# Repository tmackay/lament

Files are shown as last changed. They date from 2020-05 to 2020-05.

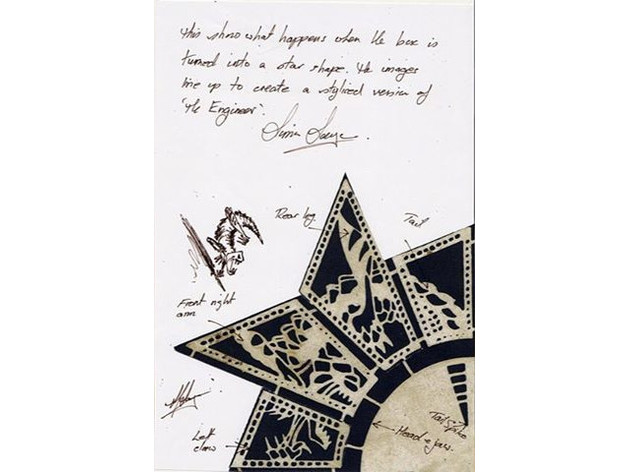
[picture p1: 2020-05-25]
sayce.jpg

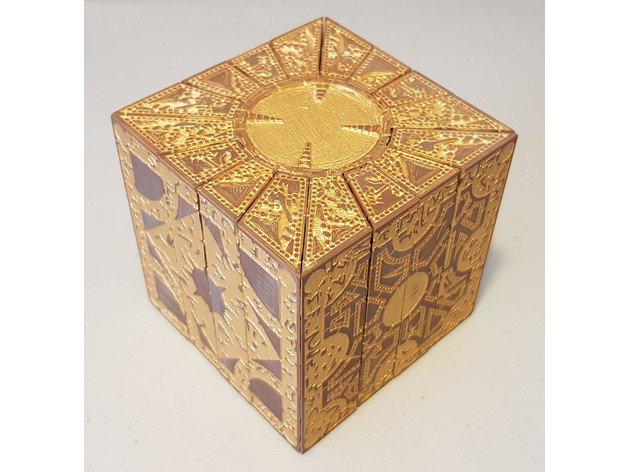
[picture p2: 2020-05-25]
painted.jpg

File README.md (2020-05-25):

# lament
Hellraiser Puzzle Box - Lament Configuration

Functioning Hellraiser inspired puzzle box using my own planetary gearbox core.

[Assembly video](https://youtu.be/JLJvNn56pJ8) - Jump to the end to see the finished product in action. Now tracking my source code in [github](https://github.com/tmackay/lament) to make tracking versions and bugs easier.

The Lament configuration - art by [artist064](https://www.deviantart.com/artist064) "The original Lament Configuration was created by [Simon Sayce](https://www.youtube.com/watch?v=OcX2sYlTq2U) for the original Hellraiser movie".

This is a slight improvement over the previous design which was only solvable by a simplistic brute force method. I have added an extra latch which must be disengaged after aligning the gears. It is also a bit of an experiment in incorporating an internal "clicker" device to indicate when the gears are (partially) aligned. There are also "false gates" which give it away by allowing the core to open slightly when aligned - without these I think it would be near impossible (CH included) unless we incorporate some other indicator (the sound of distant bells, perhaps - there is room for electronics). Also provision for an internal spring to bring the box to "life". If the "clicker" idea works out, it might be worth adding more for effect. Some aluminium strips and magnets could be included in future a future release to provide an inductive braking effect.

Print at 0.2mm (at least the core - it is designed to produce a 1-layer gap between the ring gears and is sensitive to layer height) and separate ring gears with a sharpened spatula, flat razor blade scraper, box cutter or similar. Print parts A and B separately (around 21 hours each, 8 for the core). Ease the core (wider tabs first, careful of orientation and alignment of the narrow tabs) into the end of the "claw", they will need to flex a little.

Enable Support Interface at 100%, Touching Buildplate with overhang of 85 degrees for improved finish. This will give a nice solid disk to support the raised dial for parts A and B which can be pried off. Part C does not require support. (Cura)

I'd also recommend "breaking in" the core by giving it 5 minutes on a drill or Dremel tool to spin the gears. They will be quite stiff at first but soon wear in to move freely. Similarly the sliding parts might need a light sanding or at least operated back and forth a bit to loosen them up.

Bitmaps were converted to black and white using Threshold filter in GIMP then traced using InkScape, simplified using "Flatten Bezziers" extension before being exported as SVG for import into OpenSCAD. OpenSCAD struggled importing multiple SVGs, so individual faces were added to separate cubes and combined using MeshLab ([more info](https://www.thingiverse.com/thing:4178313)).

TinkerCad was used for the final intersection (subtract the negative from the artwork cube) as everything else I tried crashed or made a mess of the mesh.

Most versions of this artwork have the gold detail raised, personally I prefer the negative as it preserves most visual detail when slicing for FDM. Painting gold followed by sanding back the raised edges allows for low painting skill required. If you'd like to try other artwork cubes, I have included the negative. Load your own cube in TinkerCad, scale as desired and subtract. The two halves can then be separated in MeshLab or similar for printing (eg. using select connected followed by delete).

I've also just realised all the artwork is in mirror image in previous versions, betrayed by "The Beautiful Woman", "The Crouching Man" et al. The orientation of the faces relative to each other is also incorrect. I have attempted to remain faithful to the original design, however it is apparent that multiple on-screen props were used with differing configurations, even some faces mirrored. To this end I have settled on the widely used [HR1 configuration by Xane](http://www.cenobite.com/box/lament/)

The latest upload is also dimensionally accurate with the original being 3" across exactly (according to the interview with Sayce) which "held some significance" as opposed to the 80mm approximations. I have also included both positive and negative versions of the artwork to cater to different painting/finishing preferences.

UPDATE: Fixed some overlap in the core which was causing it to print the planet gears fused to the ring gears more so than expected. Still working on the spring idea - will probably go back to a shorter spring contained within the center of the core.

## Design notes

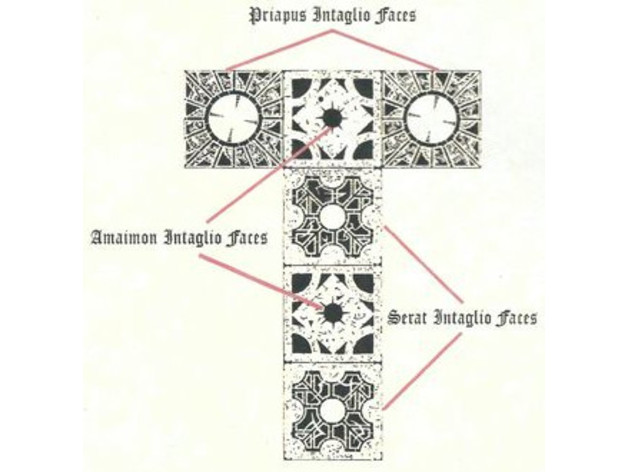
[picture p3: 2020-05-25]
flat.jpg

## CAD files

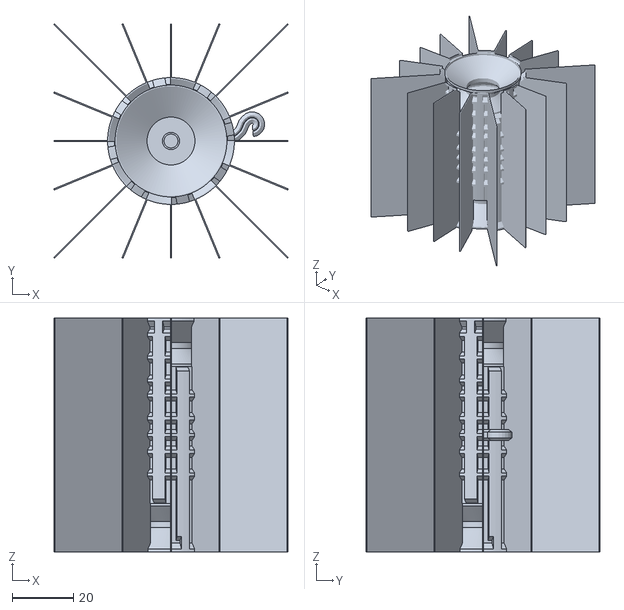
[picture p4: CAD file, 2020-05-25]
Puzzle_Cube_3x3N.stl
76.2 x 76.2 x 76.2

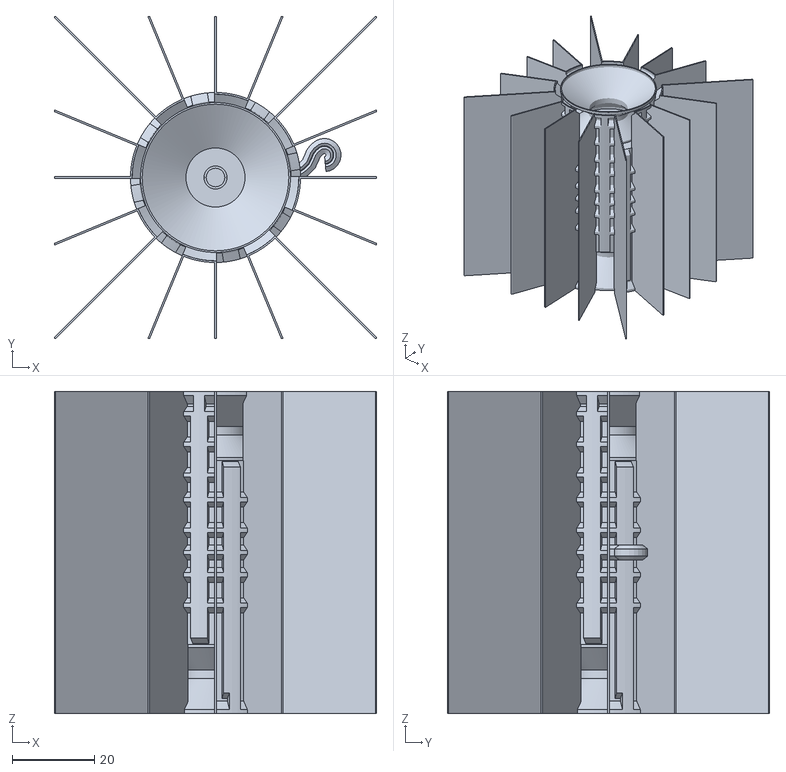
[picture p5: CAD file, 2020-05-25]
Puzzle_Cube_3x3P.stl
78.2 x 78.2 x 78.2

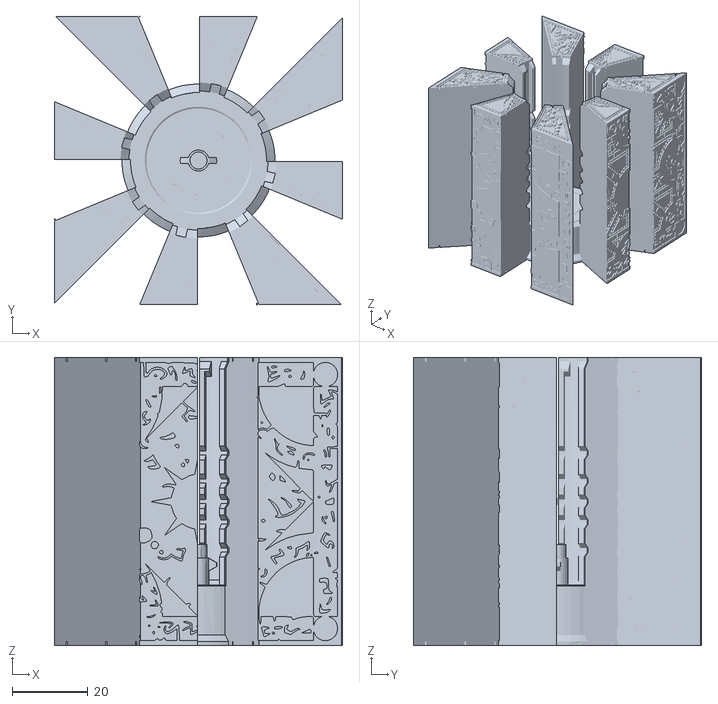
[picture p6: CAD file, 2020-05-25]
Lament_Configuration_3x3x3_Negative_B.stl
76.2 x 76.2 x 76.2

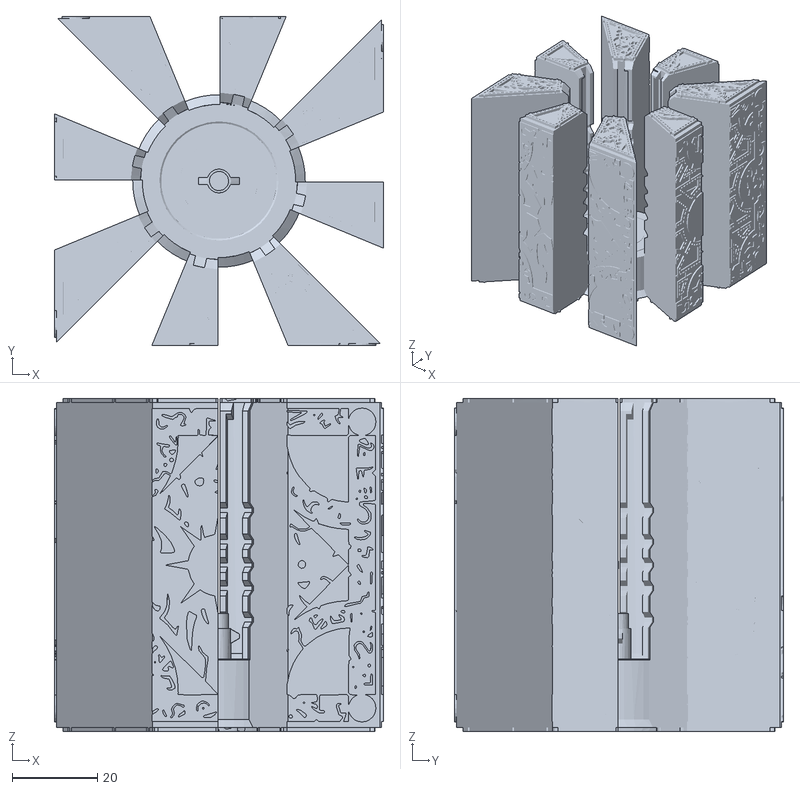
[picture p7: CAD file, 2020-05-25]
Lament_Configuration_3x3x3_Positive_B.stl
77.2 x 77.2 x 78.2

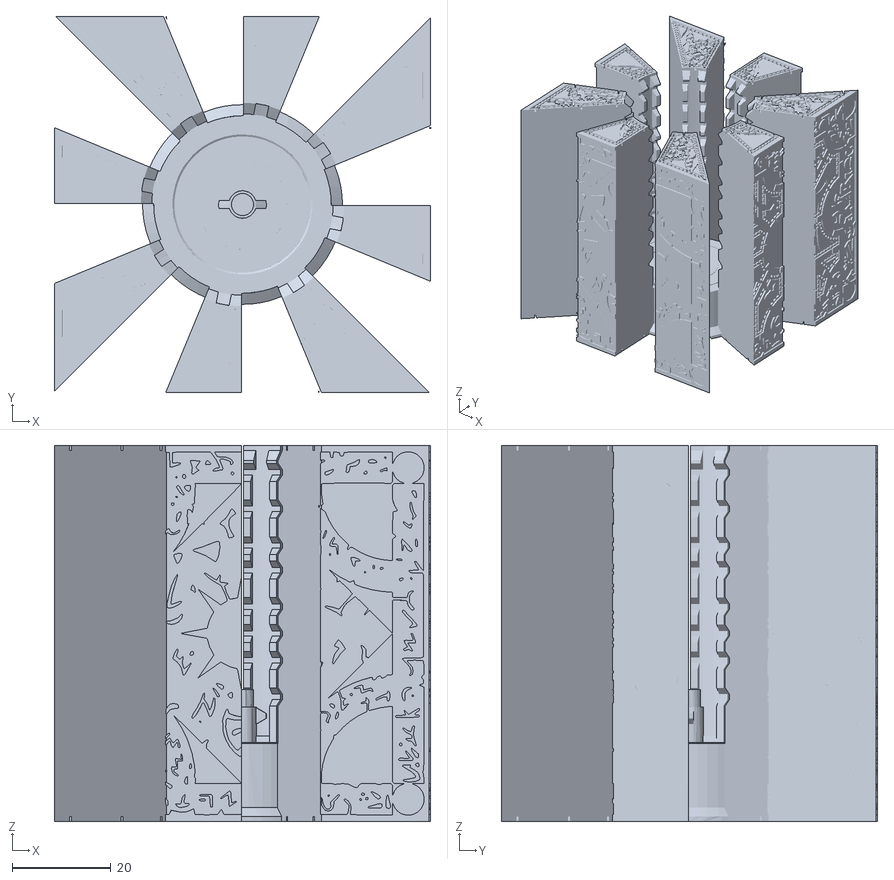
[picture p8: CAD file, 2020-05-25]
Lament_Configuration_3x3x3_Negative_A.stl
76.2 x 76.2 x 76.2

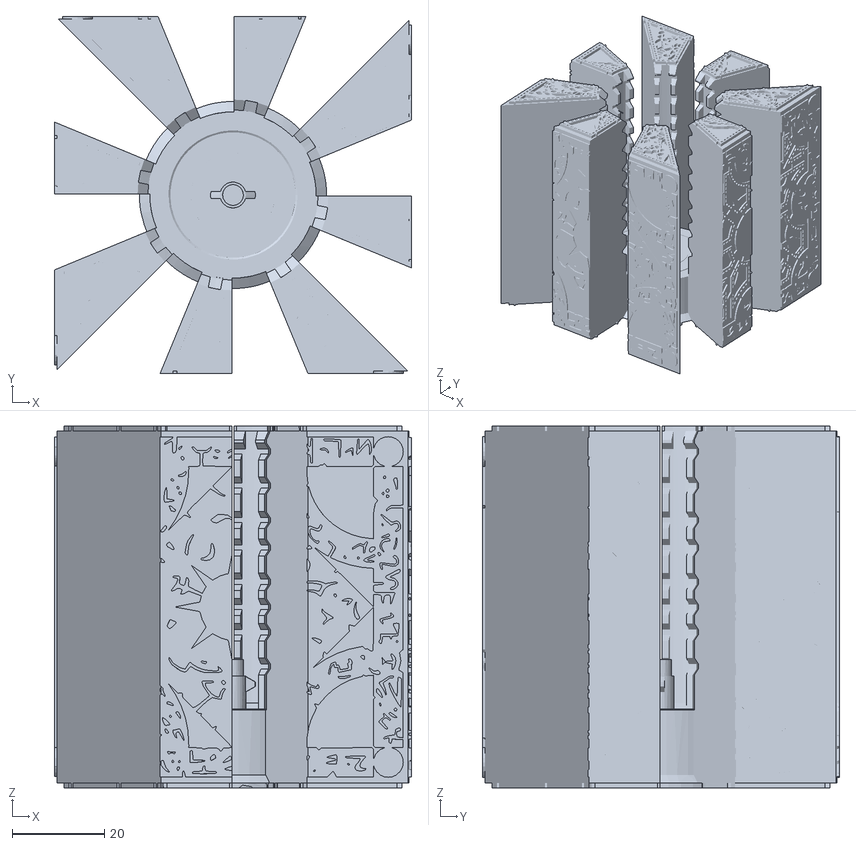
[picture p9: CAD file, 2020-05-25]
Lament_Configuration_3x3x3_Positive_A.stl
77.2 x 77.2 x 78.2

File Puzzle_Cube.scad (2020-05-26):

// OpenSCAD Compound Planetary System
// (c) 2019, tmackay
//
// Licensed under a Creative Commons Attribution-ShareAlike 4.0 International (CC BY-SA 4.0) license, http://creativecommons.org/licenses/by-sa/4.0.
//include <MCAD/involute_gears.scad> 

// Which one would you like to see?
part = "core"; // [box:Box,lower:Lower Half,upper:Upper Half,core:Core]

// Use for command line option '-Dgen=n', overrides 'part'
// 0-7+ - generate parts individually in assembled positions. Combine with MeshLab.
// 0 box
// 1 ring gears and jaws
// 2 sun gear and knob
// 3+ planet gears
gen=undef;

/*
P1	P2	R1	R2	S1=2*P1	S2=2*P2	n1	n2	Gear Ratio
8	5	34	20	16	10	-2	0	-38.66666667
8	6	34	23	16	12	-2	1	-22.23333333
8	7	34	26	16	14	-2	2	-16.75555556
*/

// Overall scale (to avoid small numbers, internal faces or non-manifold edges)
scl = 1000;

// External dimensions of cube
cube_w_ = 76.2;
cube_w = cube_w_*scl;

// Number of planet gears in inner circle
planets = 5; //[3:1:21]

// Height of planetary layers (layer_h will be subtracted from gears>0)
gh_ = [7.2, 7.4, 7.4, 7.4, 7.4, 7.4];
gh = scl*gh_;
// Modules, planetary layers
modules = len(gh); //[2:1:3]

// Number of teeth in planet gears
pt = [5, 6, 7, 7, 6, 5];
// For additional gear ratios we can add or subtract extra teeth (in multiples of planets) from rings but the profile will be further from ideal
of = 0*gh_;
// number of teeth to twist across
nt = pt/pt[0];
// Sun gear multiplier
sgm = 2; //[1:1:5]
// For fused sun gears, we require them to be a multiple of the planet teeth
dt = pt*sgm;
// Find closest ring gear to ideal
// and add offset
rt = [for(i=[0:modules-1])round((2*dt[i]+2*pt[i])/planets+of[i])*planets-dt[i]];
// Outer diameter of core
outer_d_ = 36.0; //[30:0.2:300]
outer_d = scl*outer_d_;
// Ring wall thickness (relative pitch radius)
wall_ = 3.1; //[0:0.1:20]
wall = scl*wall_;

// Hollow - might actually increase print time but could help for SLA
Hollow = 0;				// [1:Yes , 0:No]
// Box wall thickness when hollow
hol_ = 1.22; //[0:0.1:20]
hol = scl*hol_;
// Add additional thickness to allow embossed art when hollow
dep_ = 0.5; //[0:0.1:20]
dep = scl*dep_;

// Negative - tinkercad import will fill in hollow shapes (most unhelpful). This will also save a subtraction operation ie. This will give us the shape to subtract from the art cube directly.
Negative = 1;				// [1:No, 0.5:Yes, 0:Half]

// Calculate cp based on desired ring wall thickness
cp=(outer_d/2-wall)*360/(dt+2*pt);

// what ring should be for teeth to mesh without additional scaling
rtn = dt+2*pt;
// scale ring gear (approximate profile shift)
s=[for(i=[0:modules-1])rtn[i]/rt[i]];
// scale helix angle to mesh
ha=[for(i=[0:modules-1])atan(PI*nt[i]*cp[i]/90/gh[i])];
has=[for(i=[0:modules-1])atan(PI*nt[i]*s[i]*cp[i]/90/gh[i])];

// Shaft diameter
shaft_d_ = 6; //[0:0.1:25]
shaft_d = scl*shaft_d_;
// Spring outer diameter
spring_d_ = 5; //[0:0.1:25]
spring_d = scl*spring_d_;
// False gate depth
fg_ = 1; //[0:0.1:5]
fg = scl*fg_;

// secondary shafts (for larger sun gears)
shafts = 6; //[0:1:12]
// Width of outer teeth
outer_w_=3; //[0:0.1:10]
outer_w=scl*outer_w_;
// Aspect ratio of teeth (depth relative to width)
teeth_a=0.75;
// Offset of wider teeth (angle)
outer_o=2; //[0:0.1:10]
// Gear depth ratio
depth_ratio=0.5; //[0:0.05:1]
// Gear clearance
tol_=0.2; //[0:0.01:0.5]
tol=scl*tol_;
// pressure angle
P=30; //[30:60]
// Layer height (for ring horizontal split)
layer_h_ = 0.2; //[0:0.01:1]
layer_h = scl*layer_h_;
// height of rim (ideally a multiple of layer_h
rim_h=3;
// Chamfer exposed gears, top - watch fingers
ChamferGearsTop = 0;				// [1:No, 0.5:Yes, 0:Half]
// Chamfer exposed gears, bottom - help with elephant's foot/tolerance
ChamferGearsBottom = 0;				// [1:No, 0.5:Yes, 0:Half]

// Curve resolution settings, minimum angle
$fa = 5/1;
// Curve resolution settings, minimum size
$fs = 1/1;
// Curve resolution settings, number of segments
$fn=96;

// Planetary gear ratio for fixed ring: 1:1+R/S
//echo(str("Gear ratio of first planetary stage: 1:", 1+ring_t1/drive_t));

// (Planet/Ring interaction: Nr*wr-Np*wp=(Nr-Np)*wc)
// one revolution of carrier (wc=1) turns planets on their axis
// wp = (Np-Nr)/Np = eg. (10-31)/10=-2.1 turns
// Secondary Planet/Ring interaction
// wr = ((Nr-Np)+Np*wp)/Nr = eg. ((34-11)-11*2.1)/34 = 1/340
// or Nr2/((Nr2-Np2)+Np2*(Np1-Nr1)/Np1)
//echo(str("Gear ratio of planet/ring stage: 1:", abs(ring_t2/((ring_t2-planet_t2)+planet_t2*(planet_t-ring_t1)/planet_t)))); // eg. 3.8181..

// Final gear ratio is product of above, eg. 1:1298.18..
//echo(str("Input/Output gear ratio: 1:",abs((1+ring_t1/drive_t)*ring_t2/((ring_t2-planet_t2)+planet_t2*(planet_t-ring_t1)/planet_t))));

// sanity check
for (i=[1:modules-1]){
    if ((dt[i]+rt[i])%planets)
        echo(str("Warning: For even spacing, planets (", i, ") must divide ", dt[i]+rt[i]));
    if (dt[i] + 2*pt[i] != rt[i])
        echo(str("Teeth fewer than ideal (ring", i, "): ", dt[i]+2*pt[i]-rt[i]));
    if(i<modules-1)echo(str("Input/Output gear ratio (ring", i, "): 1:",abs((1+rt[modules-1]/dt[modules-1])*rt[i]/((rt[i]-pt[i])+pt[i]*(pt[modules-1]-rt[modules-1])/pt[modules-1]))));
}

g=addl([for(i=[0:modules-1])(dt[i]+rt[i])%planets],modules)?99:gen;

// Calibration cube (invalid input)
if (g==99) {
    translate(scl*10*[-1,-1,0])cube(scl*20);
}

// Tolerances for geometry connections.
AT=scl/64;
ST=AT*2;
TT=AT/2;

core_h=addl(gh,modules);
core_h2 = (cube_w-core_h)/2;

r=1*scl+outer_d/2-4*tol;
h=core_h2;
d=h/4;

// overhang test
if(g==undef&&part=="test"){
    //gear2DS(dt[0],cp[0]*PI/180,P,depth_ratio,tol,gh[1]);
    
    //gear2DS(pt[0],cp[0]*PI/180,P,depth_ratio,tol,gh[1]);
    ring2DS(rt[0],s[0]*cp[0]*PI/180,P,depth_ratio,-tol,gh[1],outer_d/2);

}

// Spring
if(g==undef&&part=="spring"){
    difference(){
        translate([0,0,core_h2-cube_w/2+tol+shaft_d+0.25*shaft_d])
            cylinder(d=shaft_d-2*tol,h=cube_w/2-core_h2-tol-1.25*shaft_d-tol,$fn=6);
        translate([0,0,-7.5*scl])cylinder(d=5*scl,h=7.5*scl);
    }
    translate([0,0,-7.5*scl])cylinder(d=3*scl,h=7.5*scl-tol);
    translate([0,0,core_h2-cube_w/2+tol+shaft_d])cylinder(d2=shaft_d-2*tol,d1=0.6*shaft_d,h=shaft_d/4,$fn=6);

    // for point of reference
    /*translate([0,0,core_h2-cube_w/2-AT])cylinder(d=shaft_d-2*tol,h=0.75*shaft_d,$fn=6);
    translate([0,0,core_h2+0.75*shaft_d-cube_w/2-AT])cylinder(d1=shaft_d-2*tol,d2=0.6*shaft_d,h=shaft_d/4,$fn=6);
    mirror([0,0,1]){
        translate([0,0,core_h2-cube_w/2-AT])cylinder(d=shaft_d-2*tol,h=0.75*shaft_d,$fn=6);
        translate([0,0,core_h2+0.75*shaft_d-cube_w/2-AT])cylinder(d1=shaft_d-2*tol,d2=0.6*shaft_d,h=shaft_d/4,$fn=6);
    }*/
}

// Spiral
if(g==undef&&part=="spiral"){
    spiral();
    //spiral_();
}

module spiral(R=2*scl+tol){
    e=1/128;
    a=41;
    d=teeth_a*outer_w;
    translate([0,d/2,0]){
        mirror([0,1,1])
            linear_extrude(2.5*d)spiral2d();
        translate([-2*R,0,0]){
            rotate_extrude(angle=a+e, convexity=10, $fn=24) // some manifold issues with this join
                translate([2*R, 0]) spiral2d();
            rotate([0,0,a])translate([4*R,0,0]){
                mirror([1,0,0])
                    rotate_extrude(angle=45, convexity=10, $fn=24)
                        translate([2*R, 0]) spiral2d();
                rotate([0,0,-45])translate([-R,0,0])
                    mirror([1,0,0])rotate_extrude(angle=205, convexity=10, $fn=24)
                        translate([R, 0]) spiral2d();
            }
        }
    }
}
module spiral_(R=2*scl+tol){
    translate([R-4*R*(1-1/sqrt(2)),4*R/sqrt(2),0])
        mirror([1,0,0])rotate_extrude(angle=205, convexity=10, $fn=24)
            translate([R, 0]) spiral2d();
    
    translate([-4*R*(1-1/sqrt(2)),4*R/sqrt(2),0])
        mirror([1,0,0])mirror([0,1,0])
            translate([-2*R,0,0])
                rotate_extrude(angle=45, convexity=10, $fn=24)
                    translate([2*R, 0]) spiral2d();
    
    translate([-2*R,0,0])
        rotate_extrude(angle=45+1/128, convexity=10, $fn=24) // some manifold issues with this join
            translate([2*R, 0]) spiral2d();
}

module spiral2d(r=gh[0]/4){
    mirror([1,1,0])scale([1,0.75,1]){
        difference(){
            translate([0,-r/2,0])circle(r=r,$fn=6);
            translate([0,r/2-tol,0])circle(r=r,$fn=6);
        }
        difference(){
            translate([0,r/2,0])circle(r=r,$fn=6);
            translate([0,tol-r/2,0])circle(r=r,$fn=6);
        }
    }
}

module click2d(r=gh[0]/4){
    mirror([1,1,0])scale([1,0.75,1]){
        intersection(){
            translate([0,r/2-tol,0])circle(r=r,$fn=6);
            translate([0,tol-r/2,0])circle(r=r,$fn=6);
        }
    }
}

// Box
if(g==0||g==undef&&(part=="box"||part=="lower"||part=="upper"))difference(){
    if(Negative)cube(cube_w,center=true);
    lament();
}
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

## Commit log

2020-05-25 fix gear helix angle
    ring gear scaling was incorrectly applied to the helix angle of the sun and planet gears
    [Puzzle_Cube.scad]
2020-05-25 fix overhang too
    [Puzzle_Cube.scad]
2020-05-26 alternate spring mount
    [Puzzle_Cube.scad]

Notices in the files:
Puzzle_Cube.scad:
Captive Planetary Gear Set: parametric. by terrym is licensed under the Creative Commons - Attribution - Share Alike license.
